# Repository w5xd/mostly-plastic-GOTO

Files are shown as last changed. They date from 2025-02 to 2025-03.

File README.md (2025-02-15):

<h1>Mostly Plastic GOTO for my Mostly Plastic Telescope</h1>

<pre>
Credits: 
    @Maff at https://kissner-optik.netlify.app/ for the Hadley and Caroline projects.
    3D model for GT2 pulleys I very slightly modified from http://www.thingiverse.com/thing:16627
    3D model for threaded screw and bolt holes using https://github.com/rcolyer/threads-scad
    the MCAD library for involute gears as distributed with Openscad
    at least one STEP model for a hardware item from http://mcmaster.com
    OnStepX at https://onstep.groups.io/g/main/wiki
    at least one STEP model for an electronic part from http://digikey.com
</pre>
Each of the above has its own license for sharing and attribution.  

This repository hosts 
the design of a GOTO stepper system for my mostly plastic 6 inch telescope, the Caroline
variant of the easy-to-build 4 inch Hadley telescope. The files here are licensed according to <a href='LICENSE'>LICENSE</a> by me, Wayne Wright. 
My GOTO design's key components are these 3D printed parts:
<ol>
<li>26:1 planetary gearbox with NEMA17 input. Printed in Prusament PC Blend
<li>200 tooth Azimuth pulley, printed in Prusament PC Blend, threaded to an M10 bolt anchored to the 
stationary plywood base of a dobson mount. 
<li>300 tooth Elevation pulley, printed in PETG, with 4 hole bolt pattern matching the Caroline rocker fasteners. 
</ol>

<h2>Introduction</h2>

I started my telescope experience with @Maff's post on printables.com: 
https://www.printables.com/model/224383-astronomical-telescope-hadley-an-easy-assembly-hig.
I first built a Hadley four inch telescope, and then its six inch Caroline variant, hoping to see some views in the night sky from my not-very-dark
suburban location. They work! Jupiter and its moons and Saturn with its rings are easily viewable from my yard with my mostly plastic telescopes. 
Now I want to find some dimmer objects. It turned out that my ability to navigate the night sky is
a limit. I recognize too few landmarks in the sky to find my way to any dimmer objects with any consistency. 
Herein is the GOTO
capability I added to my Caroline expecting its motorized mount could guide its view to, for example, Uranus, 
which I have failed
to find using manual pointing of my telescope.

To learn about motorizing it, the Hadley  discord server (https://discord.com/invite/ycaa8nX7sa) thread 
"Robo Hadley, Caroline and Bradley" has a pinned post with a design
(https://www.dropbox.com/scl/fo/ixfjrd8yioju8qfbt7a6b/AAvlGwa43vOzdwPsX5inDz8/Hadley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  login required)
involving a number of belts and pulleys and ball bearings.

But that design requires different and more sophisticated woodworking than what I already had. 
I decided to try my own that achieves, I am sure, less precision, but adequately points my Caroline
while effectively minimizing the changes to my familiar plywood Dobson mount. 
 I add (alot of) 3D printed plastic parts, including a planetary gearbox, commonly
available items like machine screws and nuts, various sizes of ball bearing assemblies and two GT2 by 10mm wide belts. 

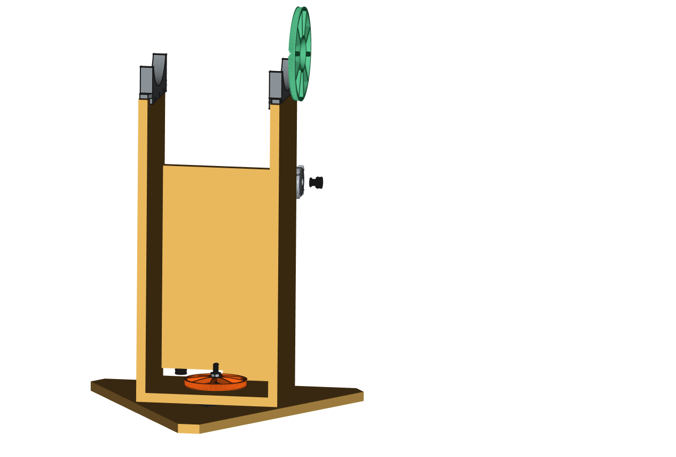
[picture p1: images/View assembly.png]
View Assembly


The plywood pieces in the drawing are from my original non-motorized mount for my Caroline. They survived intact save some
new holes.  The 3D printed cradles (in PETG) 
that mate with the Caroline's rockers are of my own design (cradle.stp) that I used on my original. Because my plywood 
cutting skills are limited, I 
tweaked the width of the cradles, printing multiple iterations, until I had a pair that held the rockers to less than about 1mm of play along
the elevation axis. In the original hand-actuated implementation the extra play was a "don't care" but I reprinted to reduce the play for the motorized version expecting
to put microswitches to trigger at the elevation limits. However, I have yet to place such limit switches as I have not found a need. The drawings above and below
emphasize the added components for GOTO capability. The elevation pulley bolts onto the Caroline original rocker arm using the original bolt pattern, 
but with longer, 10-24 x 1 1/4" bolts. The azimuth
pulley is fastened to the vertical M10 bolt that serves as the axis around which the upper box rotates.

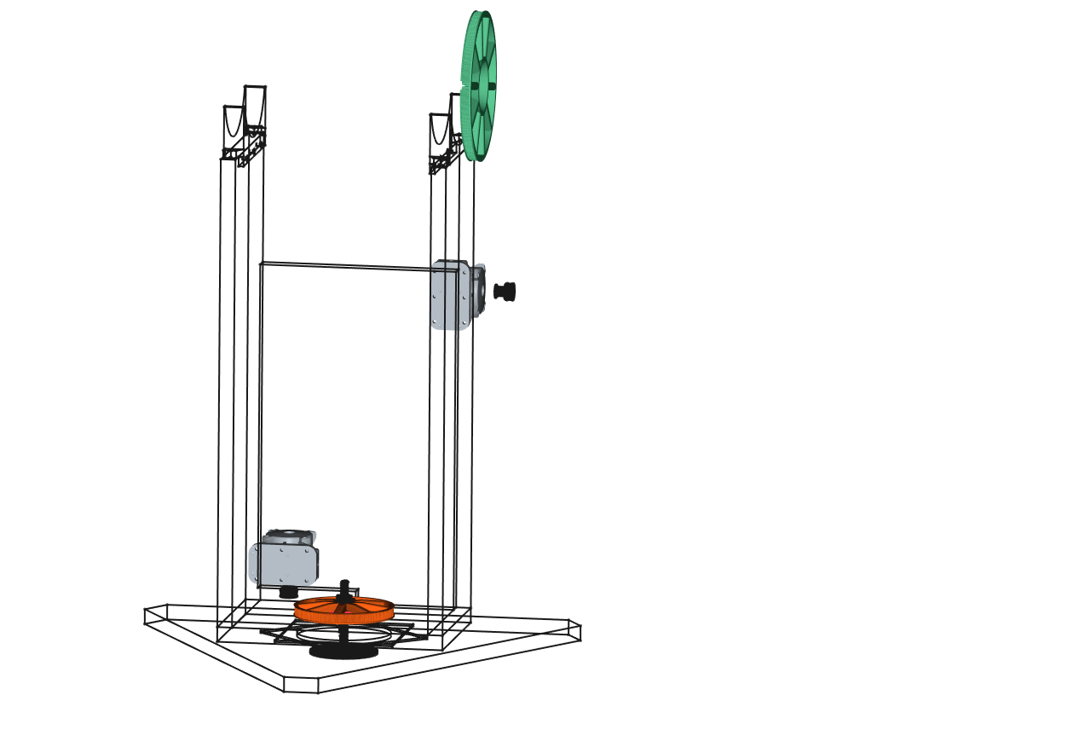
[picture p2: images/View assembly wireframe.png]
View Assembly Wireframe


The power trains for the two axes are similar to each other, but mine are not quite identical mechanically: 
each has a NEMA-17 stepper into a 3D printed 26:1 gear reduction 
box. As can be observed
in the wire frame view above, the gearboxes are mounted
to the front of the dobson mount. In my build, for the elevation axis I used a 200-step-per-revolution NEMA-17 I had left over from a 
3D printer upgrade. For
the azimuth, I bought a 400-step-per-revolution NEMA-17 from Amazon (https://www.amazon.com/dp/B0B8HB5N4S).

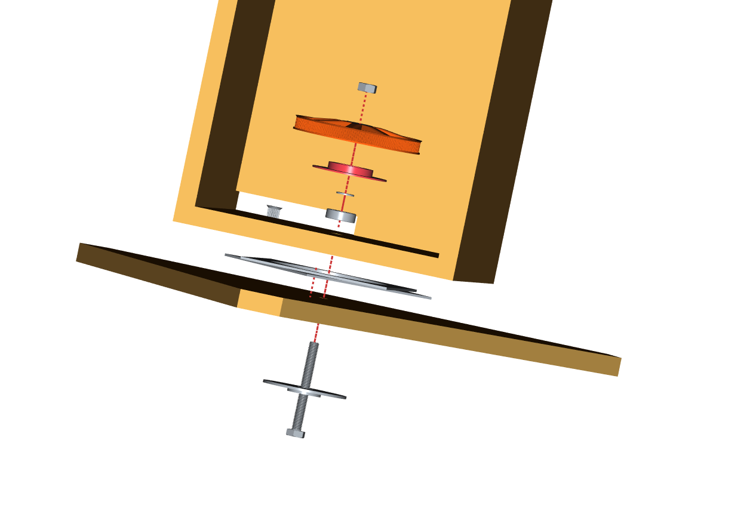
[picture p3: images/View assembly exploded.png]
View Assembly Exploded


The assembly of the azimuth axis, from the bottom up, is:
<ul>
<li>a M10 x 90mm fully threaded hex head bolt, which passes first through ...
<li>... the Azimuth Bearing M10 lock printed part.
<li>The stationary triangular plywood base
<li>An inexpensive lazy susan turntable bearing from Home Depot (https://www.homedepot.com/p/Everbilt-6-in-Square-Lazy-Susan-Turntable-with-400-lb-Load-Rating-49548/203661089)
<li>A 6200 roller bearing, 10mm ID, 30mm OD, 9mm thickness (https://www.amazon.com/dp/B07FVZMKP2)
<li>An M10 x 18mm OD x 1.5mm thick flat washer
<li>The Azimuth Bearing Holder printed part.
<li>The OnStep Azimuth Pulley printed part
<li>An M10 hex nut.
</ul>

Not shown in the drawings are the two 10mm wide GT2 belts. The elevation axis takes advantage of the fact that only a bit more than 90 degrees of
rotation are required and so can have a cut-to-length belt that is anchored in slots on the 3D printed azimuth pulley. I bought this 10mm
wide GT2 belt from Amazon and cut it: https://www.amazon.com/dp/B0CPT9J8QB

<h3>Azimuth Axis</h3>

The azimuth axis rotates all the way around therefore requires a closed loop belt. I used a 610mm by 10mm wide belt from Amazon
(https://www.amazon.com/dp/B0BYWVKM8T).

<h3>Elevation Axis</h3>
The important detail regarding the elevation pulley is that it has a tapered, GT2-compatible slot that holds the two ends of the
cut-to-length elevation pulley. 

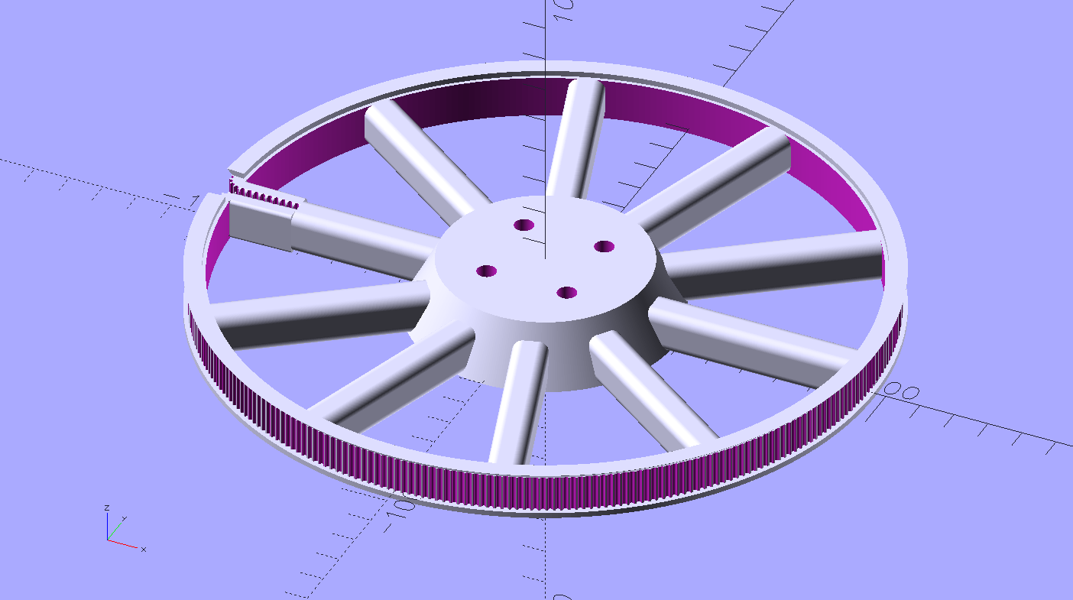
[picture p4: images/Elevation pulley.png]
Elevation Pulley


<h2>Notes for the prospective builder</h2>

As of this writing, only one of these GOTO mounts has been built: mine. The author makes no claims about how reproducible this design might be, nor for
any specifications it might meet. It worked for my own purposes. The author also makes no claims or even comments about how or whether
this design could be modified or extended, save this one: while the Hadley rocker arms have the same bolt pattern as Caroline and
therefore could mate this elevation axis unchanged, this 200 tooth azimuth pulley with its 610mm belt for the Caroline are too big to 
fit the slightly smaller plywood mount which holds my 4 inch Hadley. I have no plan
to motorize my Hadley, however, because I want to keep a telescope that doesn't require a battery.

At this time, I am not publishing printable STL files because I don't have any now that I am willing
to support or maintain over time. You will need to install and run <i>a recent version of</i> openscad to generate the printable files for the
GOTO mechanical parts. Scroll
this page https://openscad.org/downloads.html down to the Development Snapshots. (I used OpenSCAD-2024.12.04-x86-64.) The Windows cmd files to
invoke openscad with all the necessary parameter settings are published here. If you want to build from my electronics enclosure designs, then you'll
also need FreeCAD from http://https://www.freecad.org/.

As expressed in formal language in <a href='LICENSE'>LICENSE</a>, the author here places no further restrictions on anyone 
to publish derived works, <i>e.g.</i> STL files or a bill of materials for building this design. All
the sources for the 3D printable models are either of my own design and in this github repository, or are taken from somewhere that is documented
with a URL. There is more commentary in the scad files that I strongly recommend reading if you want to build this.

I describe what material I used to print each piece because I suspect that choice makes a difference in 
how some of these parts function, especially the gear box, but I don't have any recommendations about what
materials to use.

<h3>Azimuth axis assembly</h3>

My non-motorized Caroline used to turn on a 1/4-20 bolt centered through the stationary plywood base. I enlarged the existing holes for the M10 bolt in this upgrade, but I used two different twist drill sizes.
<ol>
<li>I drilled the fixed base with a 3/8" bit, which gives a tight fit to the M10 bolt, which will self-thread into the 3/8" hole.
<li>I drilled the base of the rotating plywood box with a 1/2" bit, which passes the M10 bolt without contact.
<li>The printed part, in PETG, using STL from Azimuth-Bearings.scad with its "part" set to "M10 bolt lock" tightly press 
fits over the hex head of the M10 
bolt. This bolt lock has
holes for wood screws that lock the M10 bolt hex head from turning.
<li>The lazy susan turntable needs to be centered on the M10 bolt. I designed a jig, lazy_susan_jig.scad. (This I printed in PLA--the part is
disposable.) The jig centers the turntable axis on the M10 bolt. Of course the bolt needs to already be in place in the 3/8" drilled hole for the jig
to center the turntable. I used #6 x 3/8" sheet metal screws to hold the turntable to the stationary plywood base. There are no fasteners between the 
turntable and the rotating upper plywood box. It's the M10 bolt assembly that holds the entire thing together. I left the 3D printed centering jig in place because it didn't hurt anything,
even though it is non functional once the wood screws are placed through the lazy suzan.
<li>The rotating plywood box fits loosely over the M10 bolt next.
<li>The 10MM ID bearing is next. Its ID does not fit snugly on the M10 bolt threads, but this design needs lateral stability across that axis.
Therefore, before placing the bearing, I wrapped (and wrapped and wrapped) Teflon pipe thread tape
around the mating portion of the M10 bolt to enlage its diameter to make the bearing snug.
<li>A 1.5mm thick M10 flat washer, 18mm OD goes next.
<li>The printed part using Azimuth-Bearings.scad with "part" set to "Bearing Holder" printed in PETG. It is anchored into
the plywood with three sheet metal screws.
<li>The Azimuth pulley is printed (in Prusament PC Blend) with M10 threads in its center hole. It threads onto the M10 bolt. It needs to be
tight enough to hold the stationary base to the rotating base together when the pair is lifted, but not so
tight as to apply undue pressure to the lazy suzan bearings, which makes them stickier.
<li>Finally, an M10 nut is threaded down snug against the (threaded and plastic) Azimuth Pulley. The nut is tightened enough to keep the Azimuth pulley from
unthreading when the stepper motor drives it clockwise. The metal nut against plastic threads can destroy the plastic, so I just tightened it
until the pulley didn't wiggle when I tried to turn it against the stationary base.
</ol>
Author's note on that final item: Designing M10 threads into the 3D printed pulley was the last of several failed iterations  
that tried M3 set screws
 to hold the pulley locked against the M10 bolt, <i>i.e.</i> it wasn't as easy I had hoped to lock the azimuth pulley to the fixed base's
M10 bolt.

<h3>Elevation Axis Assembly</h3>
To mount the pulley to the 'scope by removing the 4 bolts in the square pattern that hold the existing rocker,
replace the bolts with slightly longer ones, 1 1/4" long. The belt locking slot <i>must</i> be placed at the 9 o-clock position while the telescope is vertical
with the rotating part front (with the gearbox mounted) to your right.

My technique for getting the proper belt length was to first permanently mount the elevation gearbox's cleat and 
temporarily hang the gearbox on the cleat at its most vertical position. I cut a length of belt that was a couple of inches too long, and then
trimmed just a few teeth off the belt at a time until it was just long enough to enable mounting/dismounting the elevation gearbox from 
its cleat with the 8-32 x 2" tightening screw fully loosened.

<h3>3D printing</h3>
I printed all the parts of the gearbox, except its mounting cleat, using Prusament PC Blend. I also printed the azimuth pulley in PC Blend.
The rest of the parts were printed in PETG. I tried to print the elevation pulley in PC Blend, but could not overcome problems with it warping.
(It nearly fills the MK4 print bed, and I gave up when my print failed at
75% when it warped while well-bonded to the steel PEI coated sheet
and pulled the steel sheet off its magnets like a potato chip, and triggered my MK4's "filament stuck" logic--haven't seen that happen before.) 
I am using one printed in PETG. I printed all the parts on a Prusa MK4S or MK3.9S 
with a 0.4mm nozzle, and with PrusaSlicer set to 4 perimeters. I printed (almost) all the parts with a 5mm
brim. Some of the parts require a support volume when sliced, and in those cases there is an option in the scad file to
export the necessary support volume.

To successfully build the gearboxes, you <i>will</i> learn about how to confirm the correct extrusion width on your printer. If you don't already know
how, I recommend Prusa users start here: https://help.prusa3d.com/article/extrusion-multiplier-calibration_2257. Here 
is a photo of the boneyard from my gearbox printing.

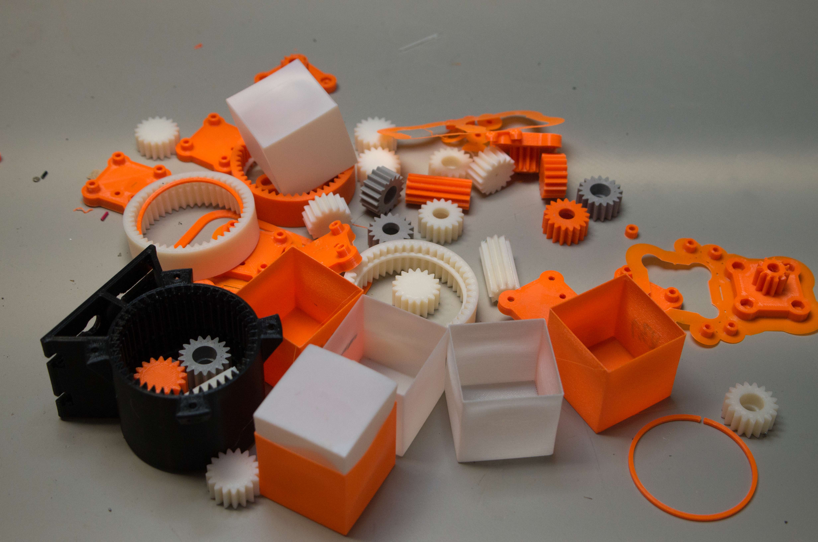
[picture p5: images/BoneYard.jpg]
Bone Yard


The scad file has an option to generate test versions of the main gearbox pieces that
have all the critical geometry and can be printed in a couple of hours. Maybe that
will help a future builder avoid further populating the plastic graveyard. See below.

Once I got my printers calibrated, the wall thicknesses of the test cube were within 5% of the required 0.45mm measurement described in the 
extrusion multiplier test. My own experience: A brand 
new "high flow" 0.40 mm nozzle came with my MK3.9S upgrade it. Nothing I did in the slicer got the test cube wall thicknesses anywhere closer 
than 10% too thick.
Finally, I swapped one of my old 0.40 mm standard brass nozzles back onto the newly upgraded printer. Then the next test print was within 5%. After that, I was able to print on both my printers without
modifying default extrusion parameters in PrusaSlicer and the gearboxes meshed well.

<h4>Gearbox</h4>

OnStepGearReducer.scad is the source for all the components of the gearbox. 
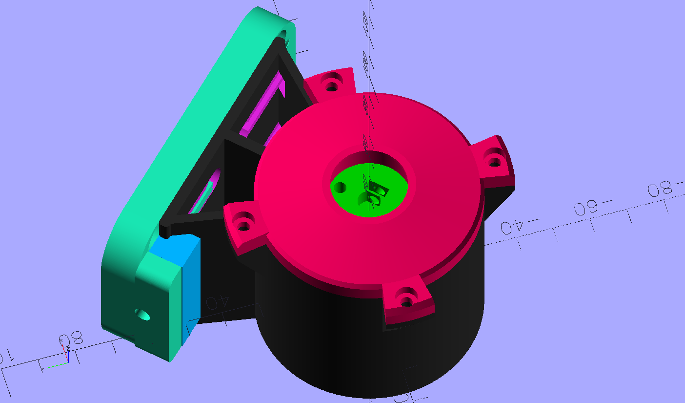
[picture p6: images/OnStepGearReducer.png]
OnStepGearReducer

MakeGearboxStl-TwoStage.cmd is a Windows batch file
that creates the various STL files from the scad. The gearbox has two internal stages, each stage giving a reduction ratio of 56:11 (or 5.0909...), 
which is about 26:1 overall. 
The scad file
has more commentary about how to print and assemble a gearbox.
The cmd file also outputs a set of four much simpler test STLs to verify printing of shapes of the outer ring, both the "planet"
and "sun" gears, the planet carrier, and the retaining ring. I found that once I could print
those test part, press the test prints and put them together and spin the gears with an appropriate amount of force,
the full feature parts would print routinely. Also in OnStepGearReducer is an option to invoke Openscad's animation feature
on the test model so you can watch the model of the gears turning. Here are the test parts:

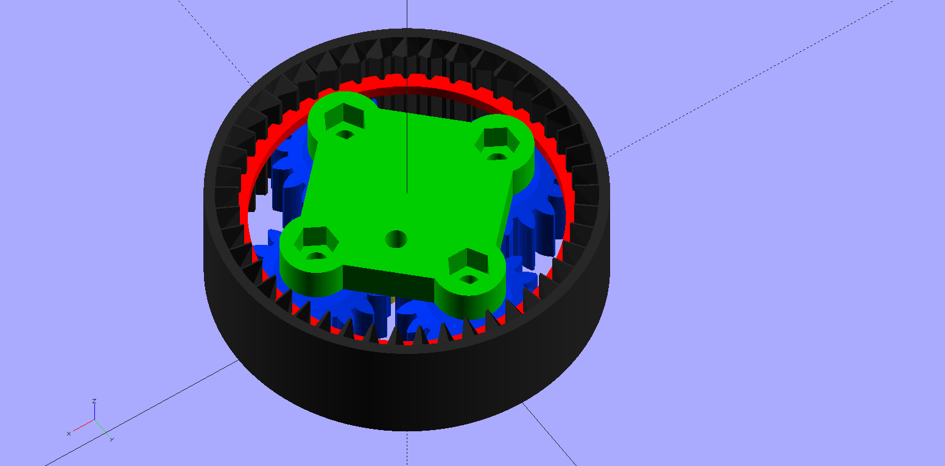
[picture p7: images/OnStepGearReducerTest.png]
Gearbox test


Each gearbox requires quantity 8 of 3mm ID by 10mm OD by 4mm thick bearing (623-2RS, https://www.amazon.com/dp/B0CLY7NJJ4). 
Each bearing is fastened by an M3 x 12mm socket head screw and M3 hex nut. And blue Locktite on the nut threads. Mine
disassembled themselves without the Locktite. After I assembled and tested that the gears would operate properly,
I disassembled and greased the plastic-on-plastic bearing surfaces with white lithium grease.

The gearbox housing is held to the cleat by the four screw heads that slide in
the gearbox slots. The printed threads are for #8 x 1/2" machine screws. 

<h4>Gearbox Output</h4>

The output of each gearbox is a length of D-profile 6mm diameter flatted shaft with a 5.5mm thickness measured to
the flattened edge. 
I bought these from Amazon and cut them to length: https://www.amazon.com/dp/B0C274W667.
The length is enough to hold the 20 tooth gearbox pulley. The STL part is from OnStepGearBoxElevationPully.scad. 
It's the same part on the azimuth gearbox as well. The inner carrier prints with a D-profile 6mm hole that should have a cut-to-length piece of steel shaft
inserted to keep it stiff against the rotational stress that it takes across the weakest grain of the
3D print.

Several M3 square nuts are required for the locking screws into the flats of the pulley shafts, and a couple of M3 socket head screws are
required. They can be set screws of at least 4mm length, but there is alternatively room for a longer socket head
screw of about 8mm. The output bearing housing, containing a 636-2Z bearing(https://www.amazon.com/gp/product/B081JSWT49), 
fastens to the outer ring with quantity four of 
M3 x 8mm socket head screws and mating M3 hex nuts. (A longer M3 screw is useful to first pull the nut into the well of the housing.)

<h2>Electronics</h2>
The electronics I used were unique to my situation. I record what I did here for completeness, but I recommend to anyone getting
this far into this project to consider using a more off-the-shelf electronics design. I bought an assembled OnStepX 
capable MaxPCB4E from https://graydigitalarts.com/product/maxpcb4e/.  I did not install the web server 
Teensy that
board supports because I only want to control my telescope from the OnStep Android app via 
Bluetooth. https://play.google.com/store/search?q=OnStep.
I bought this HC-06 bluetooth-to-serial 
device, https://www.amazon.com/dp/B07VL6ZH67, and jumpered the necessary four wires on the MaxPCB4E to it. 
The four wires are +3.3V, Ground, and TX2 and RX2 to the main Teensy 4.1 per this
diagram: https://oshwlab.com/hdutton/maxpcb4e

I did not find an appropriate enclosure for the OnStep PCB, so I designed and printed this one: OnStepEnclosureAssembly.FCStd in PETG.
I used a 9 pin Molex connector for the necessary 8 wires to the stepper motors. (Why a Molex? because I had the connectors already,
and I prefer a setup that cannot reverse the azimuth/elevation axis stepper connections.)

I decided to power my OnStep with a battery pack of eight D cells held by a pair of these
4X D-size plastic battery holders: https://www.mouser.com/ProductDetail/12BH143A-GR.
The nominal 12V DC from a full battery pack is boosted to 14V by this boost converter from Amazon. https://www.amazon.com/dp/B0C6FF1P41.
 The boost converter allows for populating the 8-position battery holder with fewer than 8 cells as long
as each cell-less position is occupied by a dummy D cell (a D-cell sized device that presents a short circuit.)
There exist 14-packs of alkaline D cells for sale, which means the booster makes it practical to use those 14 in two
batches of 7.
With my particular stepper motor amperage requirements (about 1.5A each), the internal resistance of even brand new
D alkaline cells makes six cells the fewest that will deliver the necessary amperage for that chemistry. The
boost converter also makes the system less sensitive to the battery chemistry such that, for example,
rechargeable D cells will work, and maybe fewer than eight if the builder prefers. Of course,
using fewer cells in the battery also means a shorter battery life.
The battery back and boost converter fit in this enclosure of my design: BatteryPackEnclosure.FCStd
Measured current draw at battery with boost module only: 15mA. With boost module driving the OnStep, but no steppers: 85mA.

OnStep supports limit switch input and I designed this little part, LimitSwtichBracket.FCStd, but I have not installed,
nor wired it up because I don't mind watching for a problem as the telescope moves, and,
once calibrated, OnStep won't command it to run into a stop anyway.

The electronics enclosures I printed in PETG.

If you really want to duplicate the battery enclosure, you are going to find that I am a
FreeCAD novice and ended up with a model for the enclosure base with an embedded copy of
the 3D model of the boost converter (oops.) This is error is why the part to export for the enclosure base is a
mesh "Cut" operation whose name starts with "Repaired." The power switch in the battery enclosure is the same part 
as the
slide switch in the build-it-yourself <a href='https://www.thingiverse.com/thing:3017274'>ST4 project</a> referenced below.

As I noted above, there are better designs for OnStep electronics and enclosures than mine.

<h2>Modified ST4 box</h2>
I bought a PCB for this 3D printable box for an ST4 controller: https://www.thingiverse.com/thing:3017274.
I did not like the oversized empty thickness of the bottom side of the case, so I modified it here: stl_bottom_socket.FCStd

<h2>Final assembly and disassembly</h2>

Each gearbox assembly includes a cleat with a sliding axis to adjust belt tension. The cleat has 6 available holes for fastening to the 
front of the dobson box. Both cleats are mounted to the same side, the front side, of the rotating plywood box, one
for the elevation axis and another for the azimuth. I fastened using only 3 of the 6 holes with #6 x 1" wood screws. 
Each cleat has 4 threaded holes (#8 machine screw
thread) for 8-32 x 1/2" pan head screws that form the sliding axis for the gearbox. Belt tension is maintained
 with an 8-32 x 2" screw and mating hex nut
that is anchored in a hex hole in the cleat. The tip of the belt tension screw engages a mating hole in the (poorly named)
cleat lock printed part. The elevation axis has a cut-to-length belt (GT2 by 10mm wide). 
The sliding axis on the cleats has a limited range, so it's necessary to take some care with the exact placement 
of the azimuth gearbox 
such that it is possible to both install the 610mm belt and also to tighten it enough. 
The same limited range affects the length of the cut of the elevation belt.

Unscrewing the elevation axis belt tension is how to release the elevation belt so that the
 the telescope can be separated from the mount for transport.

<h2 id="Initialize_OnStep">Initial Bench Tests and Setup with OnStepX</h2>

This project was the first time I have used OnStep. The instructions I found on its wiki most relevant for beginning testing
were here: https://onstep.groups.io/g/main/wiki/3865. However, it was not obvious to me how to accomplish
the bit it says about 
<q>If your mount doesn't have clutches and you need to use OnStep to move to the polar home position.</q>

I connected an ST4 controller, and I thought I might turn on the power
and press a button on the ST4. Nothing happens. This is by design. It takes some learning about OnStep to figure
how how to get things started. I worked out the following by trial and error, and I list below the steps I took for
future reference. Put away the ST4 controller for later use because when you start, you don't know which way its
slide switches go for forward or reverse. I follow these steps every time even though the state of the OnStep
controller when you start may allow fewer button presses, this sequence always worked, at least for me:
<ol>
<li>With the OnStep controller powered up, and with the HC06 previously initialzed
 to a known name and password (see documentation for the HC06) bring up the OnStep Android app.
<li>Use the app's drop down menu to access its "Connection" item. Expect to start with Connection every time you either power down
the OnStep controller, or return your phone from outside of Bluetooth range.
<li>If this is the first time you have connected this phone to this HC06, you'll have to choose the correct Bluetooth name and
also enter its password. If you have connected before and are using the same phone and HC06, then the Accept button is enough because
the app offers the previously connected bluetooth address.
<li>The app should now be back to its top level screen. Press its "Initialize/Park" button. and then "Set Date/Time" and 
confirm you see its "Success" response. (I installed a coin cell for the Teensy's RTC
on my PCB, but I do this Set Date step everytime anyway as it otherwise
won't find the right stars later. I need to research whether that coin cell is supposed to keep time through
the loss of 5V to the PCB.)
<li>Back button on Android to go back to the app's top level app screen.
<li>Choose "Tracking" and then "Start." Then Back button on Android to go back to top level app screen.
<li>Choose "Guide/Focus" and now (finally) we can try to make the steppers turn.
<li>Use the drop down menu to set either of the speeds with "Fast" in its name (else it will move so slowly you can't tell its moving.)
<li>Confirm that the North and South buttons move the elevation axis, respectively, up toward the zenith and down toward the horizon. 
If this
is your initial test, be especially aware of whether you might have reversed the two axis' stepper wiring with each other, 
or that you may have
wired a stepper so that it moves in the wrong direction. Get all that fixed before you go any further. Confirm that 
East/West move the
Azimuth clockwise and counter clockwise, respectively. Again, fix this before going further.
<li>Use the Guide/Focus compass direction buttons on the app (or at this point you may use the ST4 instead) to move 
the telescope
to its "polar home position" which is at the horizon pointed north.
</ol>

When I initially tested on my work bench, I kept the main mirror cover in place and used only my finder to
roughly evaluate wheter, after a "Reset to Home" in the Initialize screen, that I could use "Guide/Focus" to
move to any elevation and/or azimuth, then return to the Initialize screen to command "Return to Home" and 
confirmed through the finder that the motors in fact move it back to home. After this, I connected my ST4
and confirmed it could move the telescope, and figured out what slide switch positions correspond with
forward and reverse.

In my first few nights outside, I discovered a few other helpful hints that I had not run across elsewhere.
 While the calibration process in the OnStep app can overcome the first two out-of-level
situations below,  as a beginner I found I was way better off always setting up the telescope level this way:
<ul>
<li>Use a level on the dobson base so the upper box rotates in a (close to) horizontal plane. I permanently fastened
an inexpensive bubble level (https://www.amazon.com/dp/B09KBG2ZNL) on the triangular stationary part, and installed leveling feet on it.
<li>Use a level on the telescope to make it close to horizontal before Reset To Home on the app. I fastened an
inexpensive bubble level (https://www.amazon.com/dp/B0D7HHCY9F) to one of the 1/2" AL telescope tubes. I designed and printed
a cylindrical object that mates the ID of the AL on one side, and OD of the level on the other (ScopeLevelHolder.FCstd.)
<li>There is a "Limits" entry on the app's main menu. That is where to go to allow the elevation to point the 
telescope to objects at the zenith (where the Moon was when I first tried and OnStep refused and I didn't know why.)
</ul>

With this mostly plastic GOTO setup, I have set OnStepX  "Backlash" setting at 400" for each axis. I have
not done any detailed work to adjust this Backlash setting.

<h2>Results</h2>
I am now sure I have seen Uranus through my Caroline. Anyone with experience with small telescopes will understand why
I have to say I can't unequivocally prove it. Uranus is just a dim dot in my eyepiece as this telescope cannot resolve its disk
through my light-poluted suburban sky. My
strongest argument is that I was able to GOTO to the Moon, Venus, Saturn and Uranus this week (in early February, 2025) while they 
were all within a few dozen degrees of each other in the night sky. The GOTO well-centered the first three 
in my 9mm eyepiece, and, when I did a GOTO to Uranus, there was a dim dot in the center. Stellarium said that
Uranus would be the brightest object in my telescope's 9MM eyepiece field of view, Q.E.D.

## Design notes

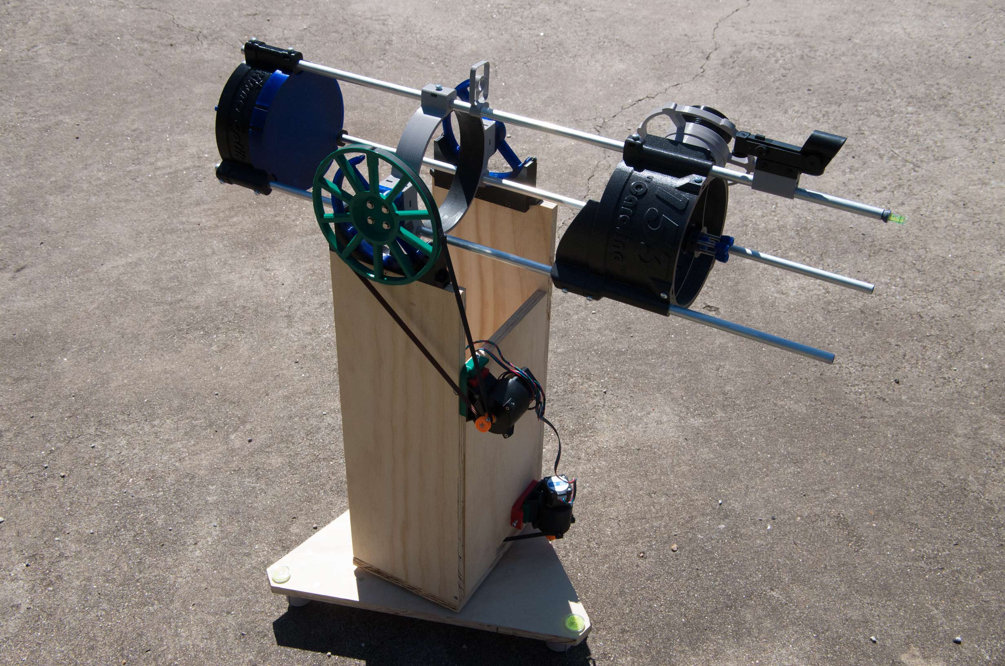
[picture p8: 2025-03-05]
images/photo-home-position-front.jpg

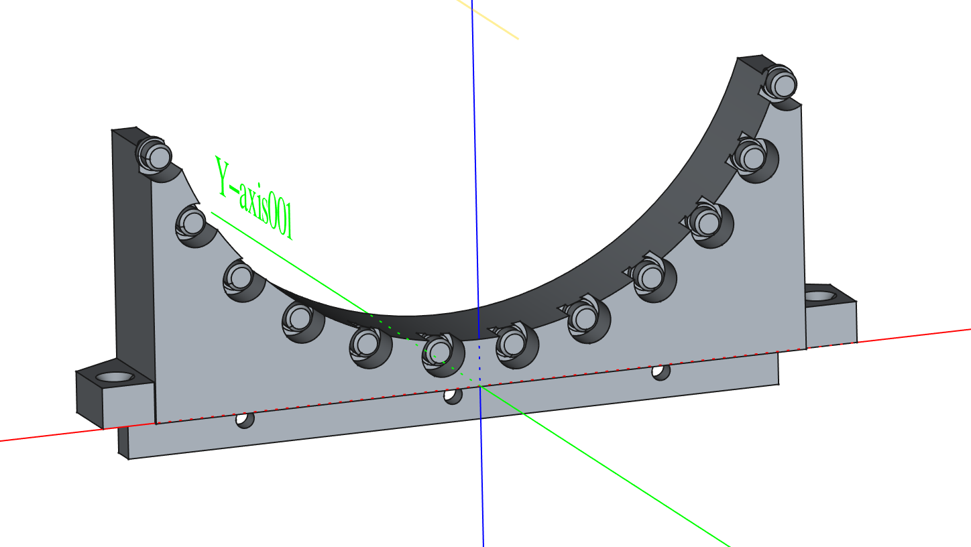
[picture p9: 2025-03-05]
images/Cradle.png

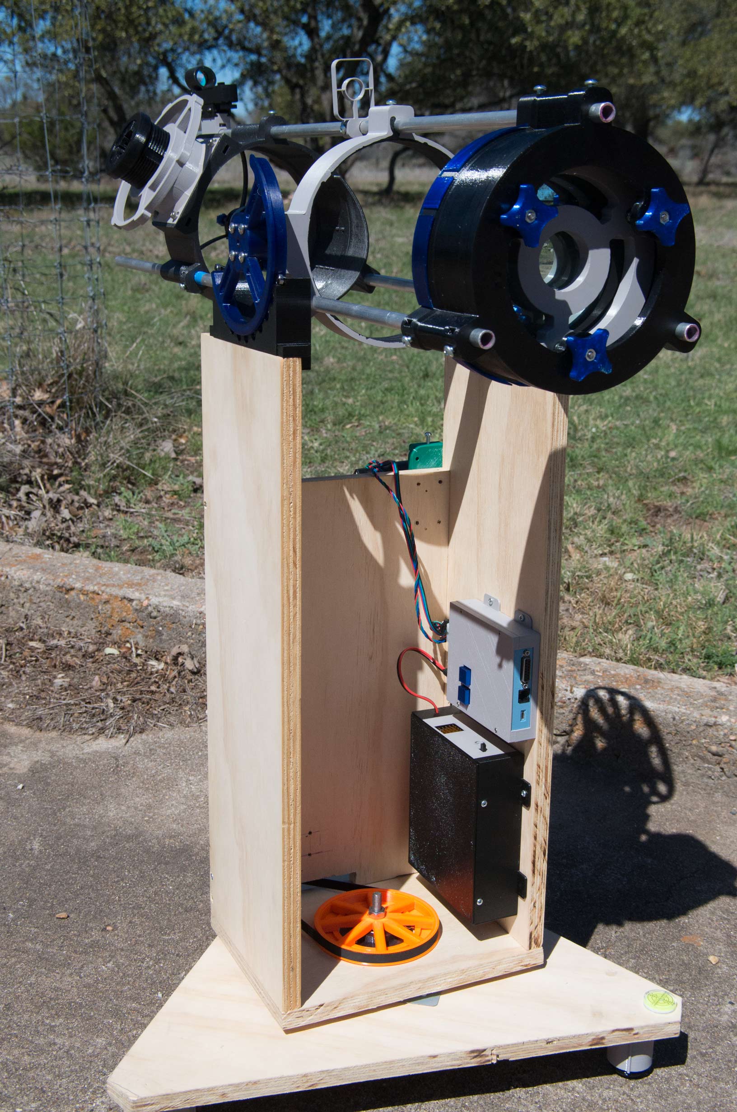
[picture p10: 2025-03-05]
images/photo-home-position-rear.jpg

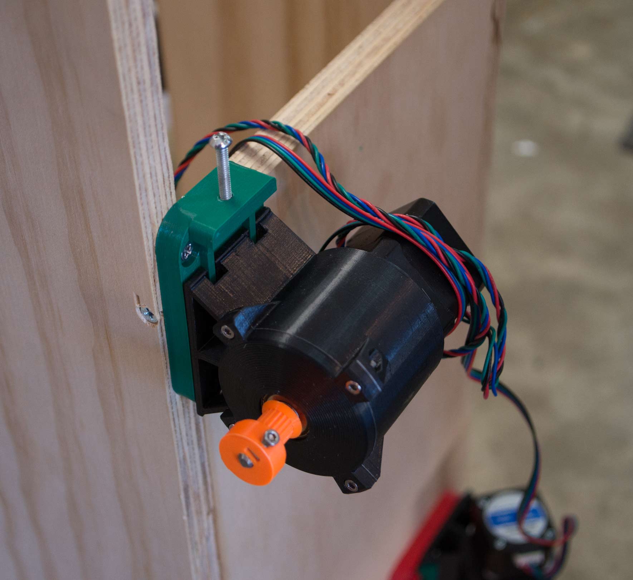
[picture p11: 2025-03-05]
images/photo-elevation-detached.jpg

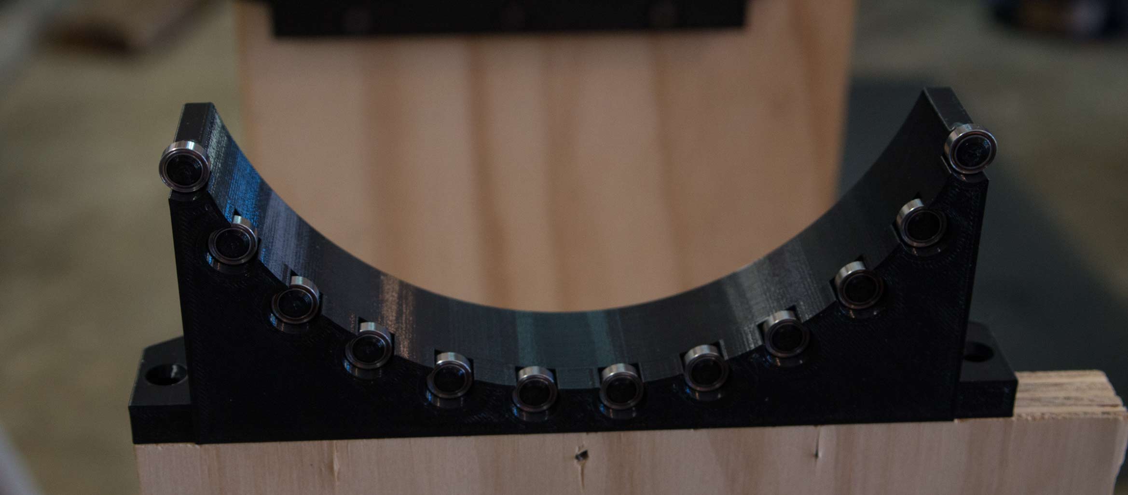
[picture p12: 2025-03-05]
images/photo-cradle.jpg

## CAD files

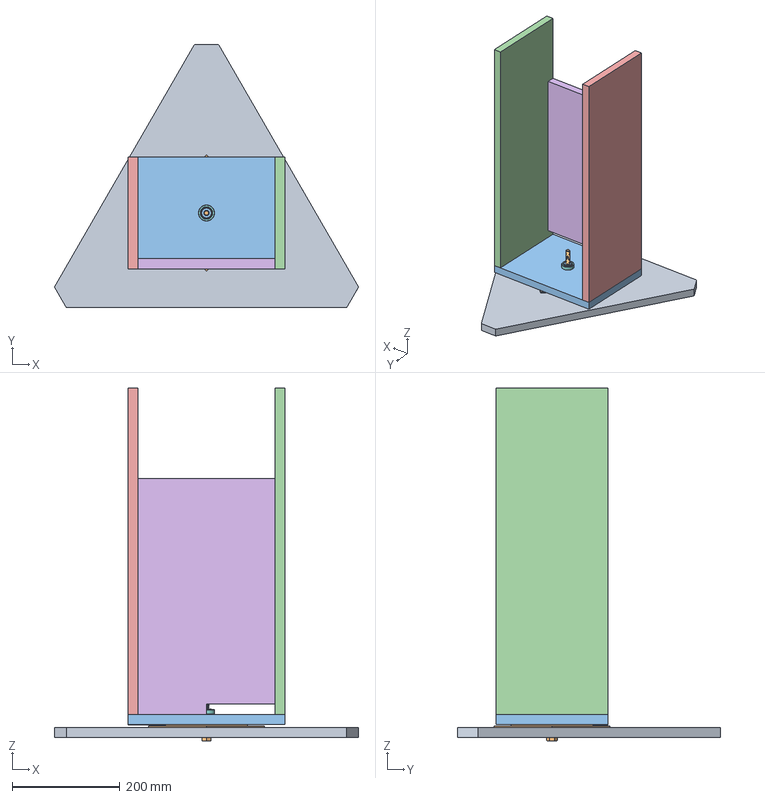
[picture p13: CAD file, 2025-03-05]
Caroline GOTO Assembly.FCStd
565.2 x 489.4 x 655.7 mm
base body
M10 x 90mm
bottom
SideR
SideL
Front
5972K101_Ball Bearing
5972K101_Ball Bearing001
5972K101_Ball Bearing002
5972K101_Ball Bearing003
5972K101_Ball Bearing004
5972K101_Ball Bearing005
5972K101_Ball Bearing006
5972K101_Ball Bearing007
5972K101_Ball Bearing008
5972K101_Ball Bearing009
5972K101_Ball Bearing010
M10 washer

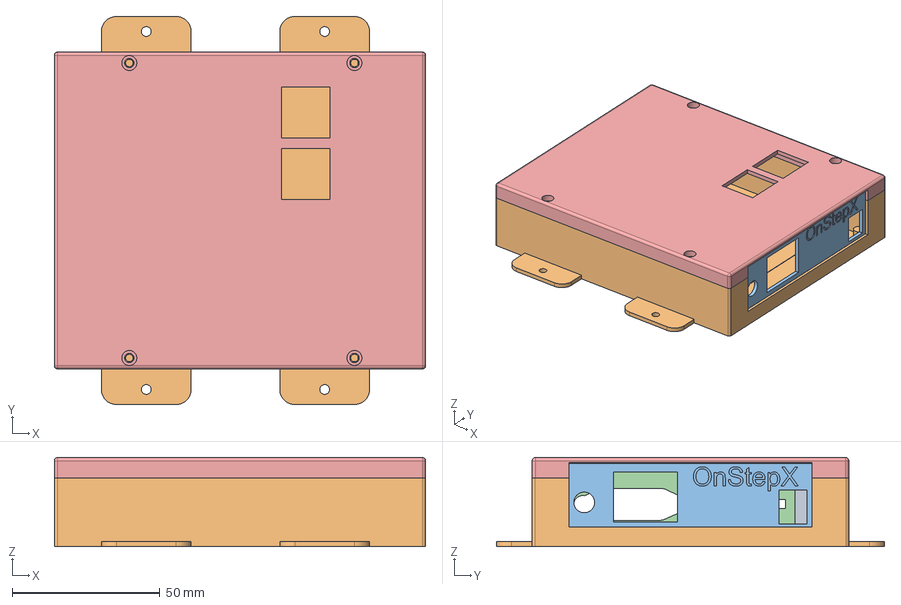
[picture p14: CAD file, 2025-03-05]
OnStepEnclosureAssembly.FCStd
125.7 x 131.3 x 30.1 mm
Fuse001
Enclosure Base
Enclosure Right
Enclosure Left
Enclosure Top

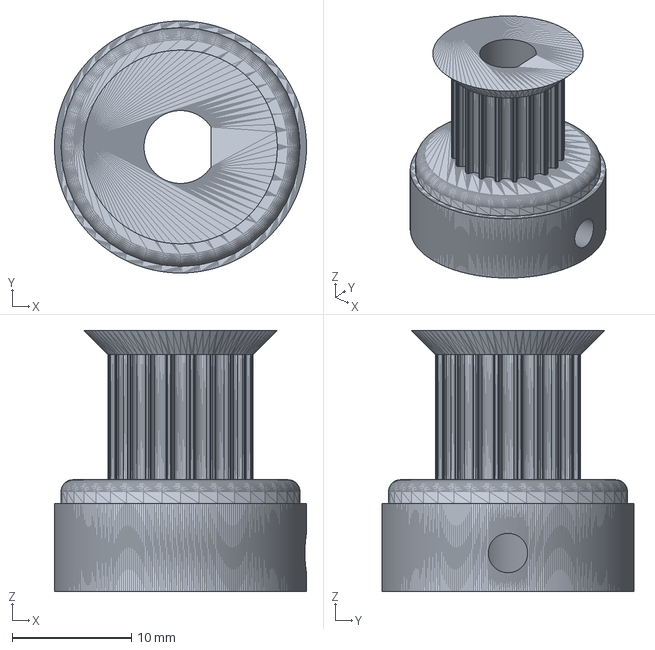
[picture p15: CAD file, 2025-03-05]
OnStepGearboxElevationPulley.FCStd
21.1 x 21.1 x 21.9 mm

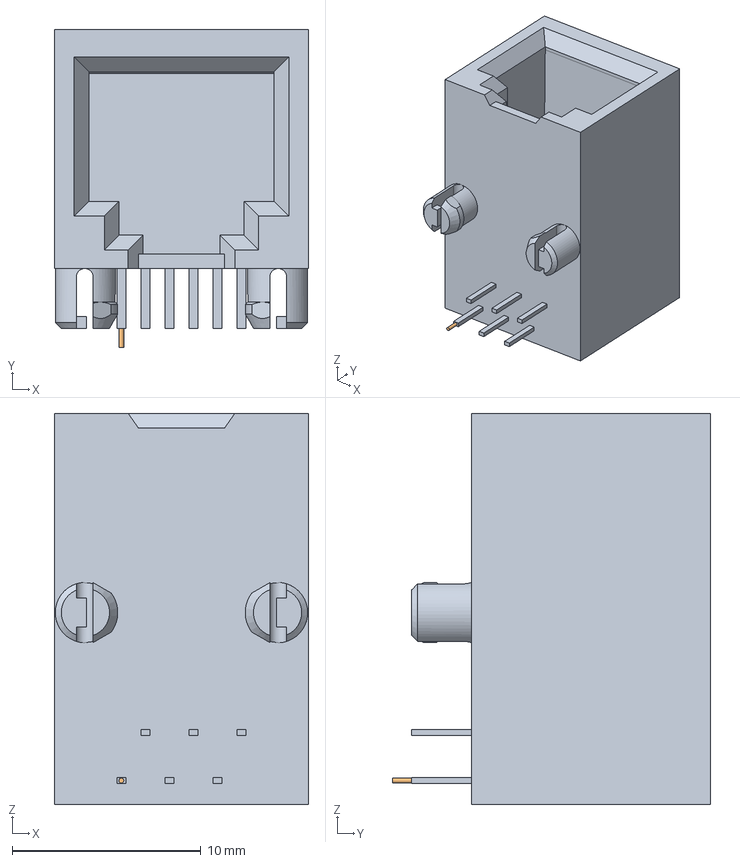
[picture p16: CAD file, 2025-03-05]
RJ12.FCStd
13.5 x 16.8 x 20.7 mm

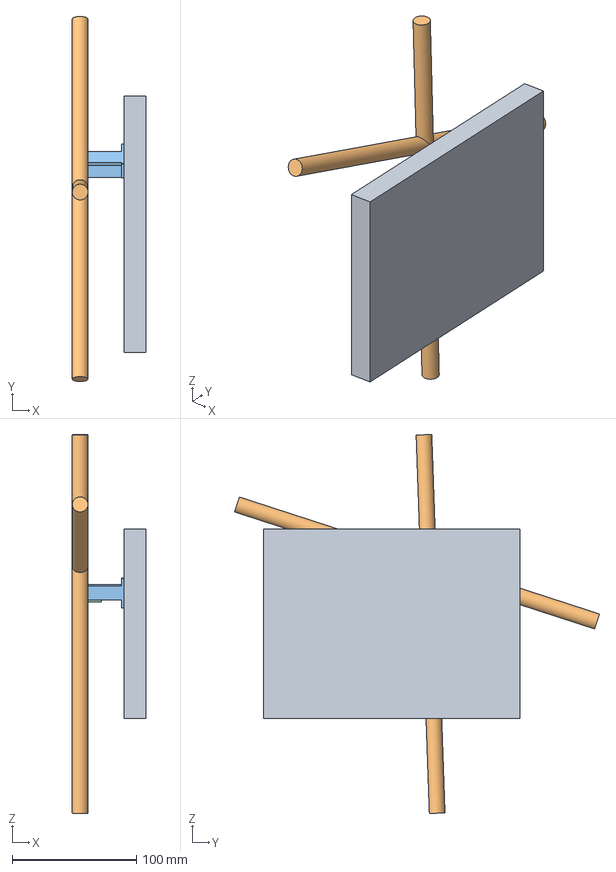
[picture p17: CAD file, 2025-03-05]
LimitSwitchBracket.FCStd
59.2 x 293.8 x 305.1 mm
Side Panel
Hadley half inch AL x 2
Bracket
Cover

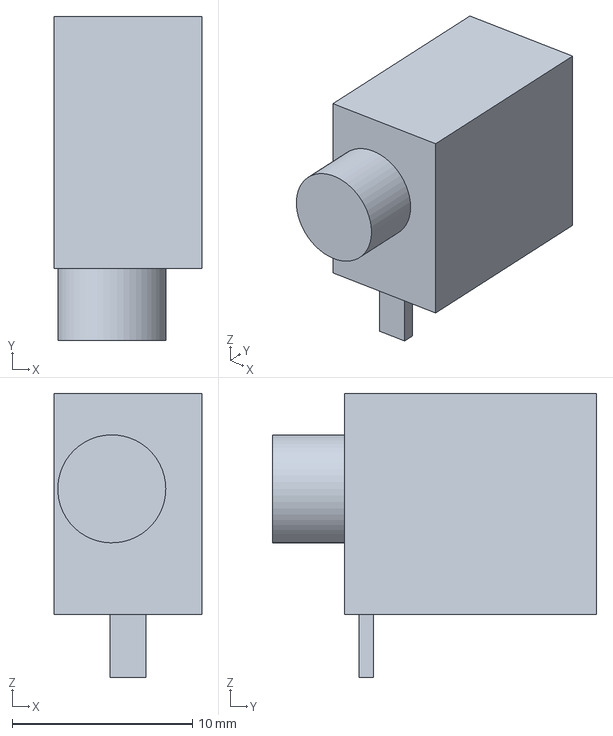
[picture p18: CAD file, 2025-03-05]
BoomEleC26230.FCStd
8.20 x 18.0 x 15.8 mm

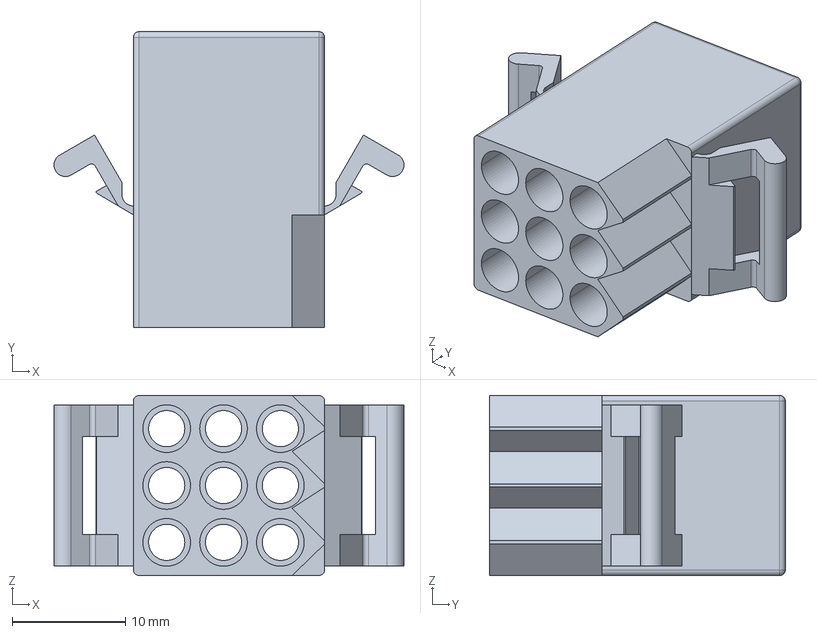
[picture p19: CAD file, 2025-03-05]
StepperMolex.FCStd
31.0 x 26.2 x 15.9 mm

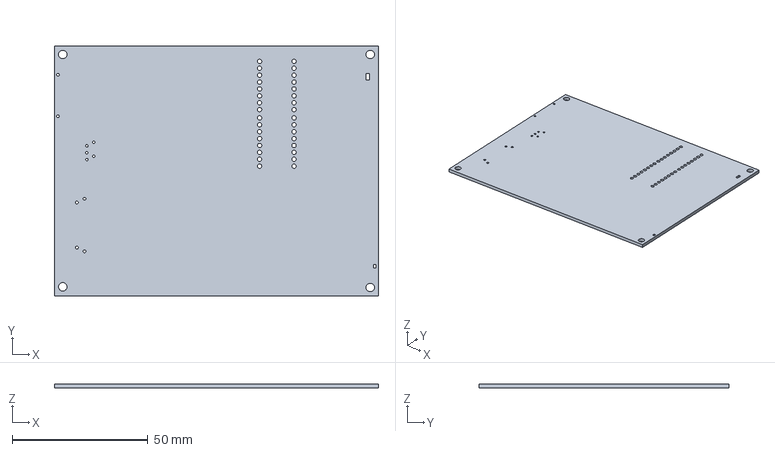
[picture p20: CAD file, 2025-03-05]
MaxPCBdxf.FCStd
119.4 x 91.9 x 1.59 mm

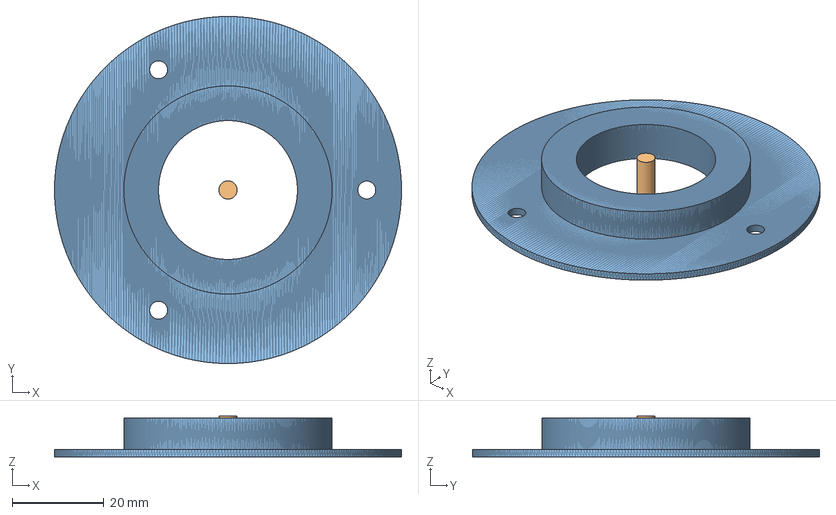
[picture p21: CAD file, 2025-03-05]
Azimuth-Bearing-Holder.FCStd
75.8 x 75.8 x 8.89 mm
Az Bearing Holder
Azimuth_Bearing_Holder001

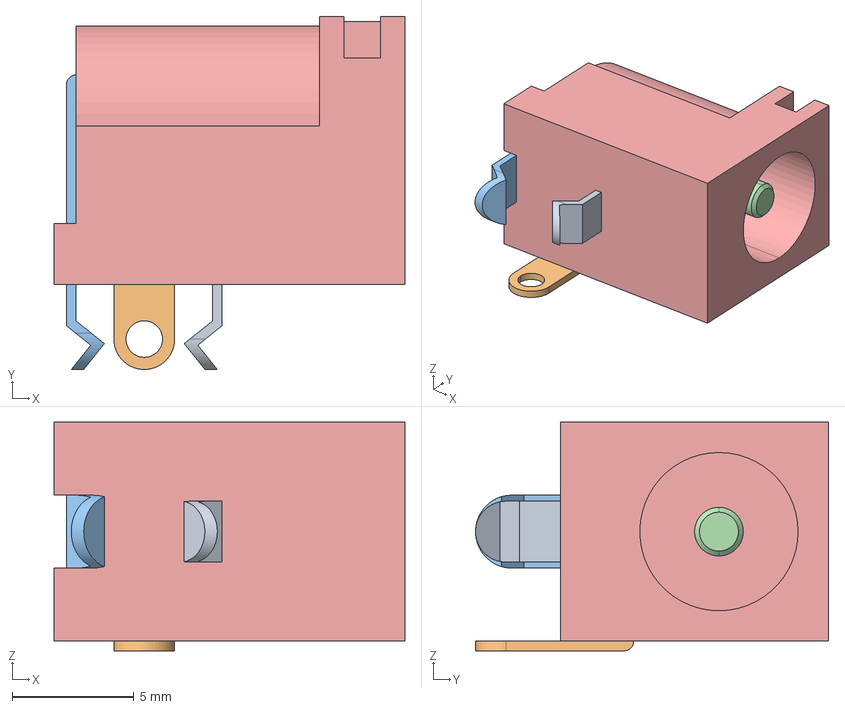
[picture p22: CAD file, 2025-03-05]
PJ202.FCStd
14.4 x 14.5 x 9.40 mm
PJ-202A_PJ-202A
PJ-202A_PJ-202A001
PJ-202A_PJ-202A002
PJ-202A_PJ-202A003
PJ-202A_PJ-202A004

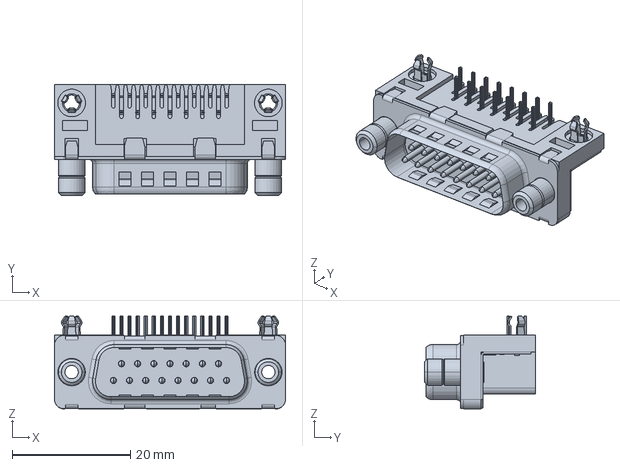
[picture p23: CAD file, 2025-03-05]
D15.FCStd
39.1 x 18.9 x 15.8 mm

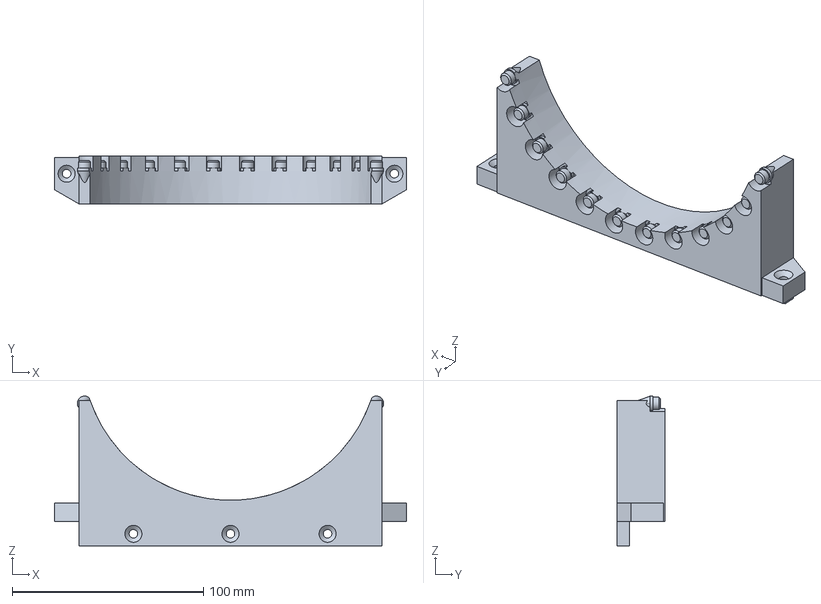
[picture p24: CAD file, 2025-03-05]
CradleBearings.FCStd
184.2 x 24.9 x 78.4 mm

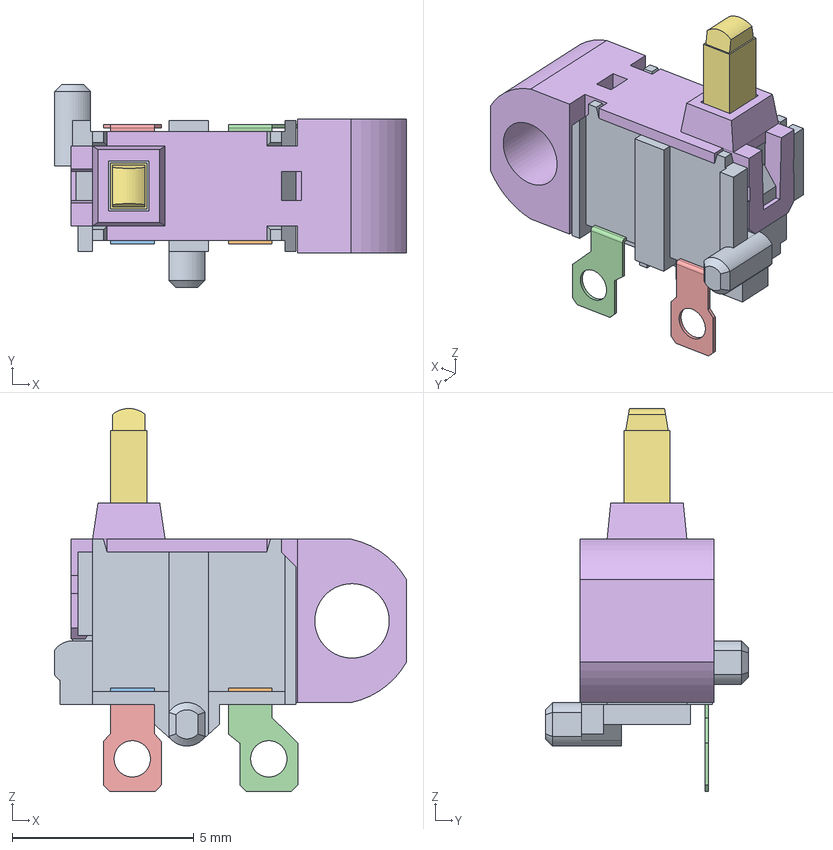
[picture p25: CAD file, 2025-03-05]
LimitSwitch.FCStd
9.70 x 5.60 x 10.5 mm
sw-3d-131-e11cs3-hs-pc-r00
sw-3d-131-e11ts8-hs-sk-r00
sw-3d-131-e11ts8-hs-sk-r001
sw-3d-131-e11ts8-hs-sk-r002
sw-3d-131-e11ts8-hs-sk-r003
sw-3d-131-e11cv9a-hs-sk-r00
sw-3d-131-e11lv9-hs-sk-r00

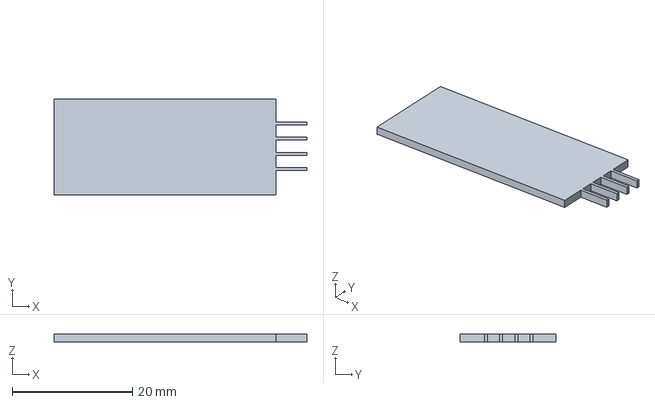
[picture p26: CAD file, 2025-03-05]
HC06.FCStd
42.1 x 16.0 x 1.27 mm

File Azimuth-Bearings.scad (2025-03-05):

/**************************************************************************
   Azimuth bearings (c) 2025 by Wayne E Wright,
   https://www.thingiverse.com/wwrr55
   is licensed under Attribution-ShareAlike 4.0 International. To view a
   copy of this license, visit
   http://creativecommons.org/licenses/by-sa/4.0/
*****************************************************************************/

echo("Azimuth-Bearings.scad version 1.0");

/* Printable parts for the Azimuth bearings on a Hadley telescope.
** They are fasteners and supporting mounts for a two-part plywood mount of the sort shown in this video:
** https://hackaday.com/2022/11/04/3d-printed-newtonian-telescope-has-stunning-looks-hadley-breaks-the-bank/
** The plywood parts are (a) the base that sits on the ground and (b) the upper part that turns 
** as the telescope moves in the azimuth direction. In the video above, the building uses a lazy susan
** bearing. 
**
** The bearing design here is not of the lazy susasn design. It instead offers a mount point for
** a pully to install an OnStep-based mechanism for a stepper motor to rotate in azimuth.
** The plywood parts here, instead of the lazy susan, simply have a drilled center hole in the two
** parts. The center hole in the plywood base is drilled for a tight fit for an M10 bolt, and
** the corresponding center hole in the rotating part of the mount is a larger hole, 0.5", to pass
** that same center bolt allowing the top to rotate w.r.t. the bottom.
**
** The weight of the upper dobson rests on 3 x teflon pads (1" x 1" x 1/8" thick).
** The M10 bolt resists lateral movement and supplies axial force only when the mount is lifted
** to be carried, in which case it transfers the weight of the base as an axial load on the 6200 bearing.
** 
** Three parts to print. Bottom to top:
** 1) a lock insert for the head of the M10 bolt to keep it from turning. Fastens to the bottom of the base.
** 2) Mounting template for the three 1" x 1" x 1/8" teflon pads. This template also has a tight-fitting
** center hole to locate the M10. Fastens to the top of the base.
** 3) Mounting template for the 6200 bearing. Fastens to the top of bottom part of the rotating azimuth
** plywood. 
*/


part = 0; // [0:M10 bolt lock, 1:Teflon Skid Template, 2: Bearing Holder]

lockBoltAcrossFlats_mm = 17;
lockBoltHeadThick_mm = 6.6;
lockBoltr_mm = lockBoltAcrossFlats_mm / (cos(30) * 2);
lockBolt_scale = (lockBoltAcrossFlats_mm - .25) / lockBoltAcrossFlats_mm;
lockScrewDiameter_mm = 3.9;

teflonPadWidthmm = 25.9;
teflonPadHeightmm = 25.9;
teflonSkidToCenter = 0.5 * 5 * 25.4;
teflonPadThick = 25.4 / 8;
teflonSkidThick = teflonPadThick /2;
teflonSkidHorzWidth = 25.4 / 4;
teflonSkidSpokeWidth = 20;
teflonSkidVerticalGap_mm = 0.5;
teflonSkidBoltClearance_mm = 9.9;

bearingOD = 30.3;
bearingThickness = 9;

module __no_more_customizer() {}

$fa = $preview ? 15 : 1;
$fs = $preview ? 3 : .1;

module M10HeadLock ()
{
    difference()
    {
        lockThick1 =  floor(lockBoltHeadThick_mm);
        lockThick2 = 25.4 / 10;
        union()
        {
            cylinder(d = 2 * lockBoltAcrossFlats_mm, h = lockThick1);
            cylinder(d = 5 * lockBoltAcrossFlats_mm, h = lockThick2);
        }
        profile = lockBoltr_mm * [for (i = [0:1 : 5], a = i * 60)[sin(a), cos(a)]];
        translate([0,0,-.1])
            linear_extrude(height = lockThick1+.2, scale = lockBolt_scale)
                polygon(profile);
        // screw holes to mount
        for (a = [0,120,240])
            rotate([0,0,a])
                translate([lockBoltAcrossFlats_mm*2.1, 0, -0.1])
                    cylinder(h=lockThick2 + 0.2, d=lockScrewDiameter_mm);
    }
}

module TeflonSkidTemplate()
{
    difference()
    {
       union()
       {         
        linear_extrude(height = teflonPadThick - teflonSkidVerticalGap_mm)
            circle(teflonSkidSpokeWidth);
        for (a = [0,120,240])
            rotate([0,0,a])
                translate([teflonSkidToCenter, 0 ])
                difference()
                {
                    union()
                    {
                     translate([-teflonSkidToCenter, -teflonSkidSpokeWidth /2])
                        linear_extrude(height = teflonSkidThick)
                            square([teflonSkidToCenter, teflonSkidSpokeWidth]);
                        linear_extrude(height = teflonPadThick - teflonSkidVerticalGap_mm)
                            offset(teflonSkidHorzWidth)
                            square(teflonPadWidthmm, center = true);
                    }
                    translate([0,0,-.1])
                    {
                        linear_extrude(height = teflonPadThick)
                            square(teflonPadWidthmm, center = true);
                        translate([-teflonPadWidthmm,0])
                            cylinder(d=lockScrewDiameter_mm, h=teflonPadThick);
                    }
                }
        }
        translate([0,0,-.1])
            cylinder(d=teflonSkidBoltClearance_mm, h=teflonPadThick);
    }
}

module Bearing6200Holder()
{
    holderThick1 = bearingThickness - 0.5;
    holderThick2 = 25.4 / 16;
    difference()
    {
        union()
        {
            cylinder(d = 1.5 * bearingOD, h = holderThick1);
            cylinder(d = 2.5 * bearingOD, h = holderThick2);
        }
        translate([0,0,-.1])
            cylinder(d = bearingOD, h = holderThick1 + .2);
        for (a = [0,120,240])
            rotate([0,0,a])
                translate([bearingOD, 0, -0.1])
                    cylinder(h=holderThick1 + 0.2, d=lockScrewDiameter_mm);
    }
}


if (part == 0)
    M10HeadLock();
else if (part == 1)
    TeflonSkidTemplate();
else if (part == 2)
    Bearing6200Holder();

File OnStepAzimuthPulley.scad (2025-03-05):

/**************************************************************************
   OnStepAzimuthPulley (c) 2025 by Wayne E Wright,
   https://www.thingiverse.com/wwrr55
   is licensed under Attribution-ShareAlike 4.0 International. To view a
   copy of this license, visit
   http://creativecommons.org/licenses/by-sa/4.0/
*****************************************************************************/

use <Pulley_Helpers.scad>
use <./libraries/threads.scad> // https://github.com/rcolyer/threads-scad

part=0; // [0:main, 1:support]

teeth = 200;
Azimuth_Bearing_Hub_Diameter_bottom_mm = 25;
Azimuth_Bearing_Clearance_Z_mm = 8;
Azimuth_Bearing_Clearance_Radius_mm = 40;

Hub_lock_screws = false;

Central_Height_z_spacer_mm = 0;
outer_rim_radial_thickness = 5;
number_of_spokes = 8;
pulley_teeth_height_mm = 10.5;
bearing_hole_diameter_mm = 9.9;
hub_extra_height_mm = 4;
hub_lock_screw_hole_diameter_mm = 3.2;
hub_lock_nut_side_mm = 5.9;
hub_lock_nut_thickness_mm = 2.6;
hub_lock_socket_diameter_mm = 6;
module __no_customizer() {}

$fa = $preview ? 20 : 1;
$fs = $preview ? 5 : 0.1;

mm_per_inch = 25.4;

base_height = mm_per_inch / 16;
alt_idler_height = base_height;
alt_base_diameter = 2 + (teeth * 2 / PI);
alt_base_cut_diameter = (teeth * 2 / PI) - 2 * outer_rim_radial_thickness;

Central_Bearing_wall_thickness_mm = 25.4 / 5;
central_height = Central_Height_z_spacer_mm + base_height + alt_idler_height + pulley_teeth_height_mm + hub_extra_height_mm;

echo(str("Full height = ", central_height / mm_per_inch, " in."));

spoke_width_mm = 10;
spoke_rounding_radius_mm = 3;

stlSolidBodymm = 0.01;

if (part == 0)
    main();
else
{
    translate([0, 0, 1])
        cut_space_for_bearing();
}

function rot_angle_from_omit(teeth, omit) = omit * 180 / teeth;

module pulleyBase(teeth, rim_mm, height, omit = 0)
{
    difference()
    {
        // pulley main
        rotate([0, 0, 180 + rot_angle_from_omit(teeth, omit)])
            rotate_extrude(angle = (teeth - omit) * 360 / teeth, $fa = 180 / teeth)
            translate([pully_OD(teeth) / 2 - rim_mm, 0])
                square([rim_mm, height]);
        // cut teeth out of pulley     
        rotate([0, 0, 270 + (omit + 1) * 180 / teeth])
            translate([0, 0, -stlSolidBodymm])
            linear_extrude(height = height + 2 * stlSolidBodymm)
                cut_teeth_from_pulley(teeth, omit = omit);
    }
}

module hub_lock_cuts()
{
    if (Hub_lock_screws)
        rotate([0,90,180 + 180/number_of_spokes])
        {
            cylinder(d=hub_lock_screw_hole_diameter_mm, h=Azimuth_Bearing_Clearance_Radius_mm);
            translate([0,0,bearing_hole_diameter_mm*1.5])
                cylinder(d=hub_lock_socket_diameter_mm, h=Azimuth_Bearing_Clearance_Radius_mm);
            extend_beyond_hub_surface = 10;
            translate([-extend_beyond_hub_surface/2,0,bearing_hole_diameter_mm*.85])
                cube(center=true,[hub_lock_nut_side_mm+extend_beyond_hub_surface, hub_lock_nut_side_mm, hub_lock_nut_thickness_mm]);
        }
}

module cut_space_for_bearing()
{
    translate([0,0,-base_height-.01])
        cylinder(h=Azimuth_Bearing_Clearance_Z_mm, r=Azimuth_Bearing_Clearance_Radius_mm);
}

module main() {
    intersection()
    {
        difference()
        {
            ScrewHole(10, central_height + .02)
            {
                difference()
                {
                    union()
                    {
                        // pulley with teeth
                        pulleyBase(teeth, outer_rim_radial_thickness, pulley_teeth_height_mm);
                        // base
                        translate([0, 0, -base_height])
                            cylinder(h = base_height, d = alt_base_diameter);
                        // idler
                        chamfer = 1.5;
                        rot_profile = [[0, 0], [outer_rim_radial_thickness - chamfer, 0], 
                                [outer_rim_radial_thickness, chamfer], [outer_rim_radial_thickness, alt_idler_height], 
                                [0, alt_idler_height]];
                        translate([0, 0, pulley_teeth_height_mm])
                            rotate_extrude(angle = 360)
                            translate([alt_base_diameter / 2 - outer_rim_radial_thickness, 0])
                            polygon(rot_profile);
                    }
                 }
                translate([0, 0, -base_height])
                {
                    // central bearing
                    difference()
                    {
                        union()
                        {
                            spoke_lift = hub_extra_height_mm + pulley_teeth_height_mm / 2;
                            tilt = atan((2 * spoke_lift)/pully_OD(teeth) );
                            linear_extrude(height = central_height)                              
                                circle(d = Azimuth_Bearing_Hub_Diameter_bottom_mm);
                            translate([0,0, spoke_lift])
                            for (spoke = [0:1 : number_of_spokes - 1])
                            {
                                rotate([0, 0, spoke * 360 / number_of_spokes])
                                {
                                    rotate([0, -90 - tilt, 0])
                                        linear_extrude(height = alt_base_cut_diameter / 2)
                                        translate([0, -spoke_width_mm / 2])
                                        offset(spoke_rounding_radius_mm)
                                        offset(-spoke_rounding_radius_mm)
                                        square([pulley_teeth_height_mm + base_height, spoke_width_mm]);

                                }
                            }
                            spoke_match_radius_mm = Azimuth_Bearing_Clearance_Radius_mm + 6;
                            cylinder(h=3*base_height, r=spoke_match_radius_mm);
                        }
                    }
                }
            } 

            cut_space_for_bearing();
            translate([0,0,-base_height-.01])
            {
                //cylinder(h=central_height + .02, d=bearing_hole_diameter_mm);
                translate([0,0,central_height])
                    cylinder(h=100, r=Azimuth_Bearing_Clearance_Radius_mm);
                translate([0,0,central_height- 1.2 * hub_lock_screw_hole_diameter_mm])
                {
                    hub_lock_cuts();
                    rotate([0,0,90])
                        hub_lock_cuts();
                }
            }
        }
    }
}

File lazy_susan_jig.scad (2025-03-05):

module no_more_customizer() {}
$fa = $preview ? 15 : 1;
$fs = $preview ? 3 : .1;

mmPerInch = 25.4;

mount_hole_diameter_mm = 10 - .1;
mount_brace_diameter_mm = 1 * mmPerInch;
mount_brace_height = mmPerInch * 3/32;
skid_pad_thickness_mm = mmPerInch * .3; 
skid_pad_radial_from_center = 3 * mmPerInch;
spoke_width = 0.5 * mmPerInch;

dolly_ID = 4.74;
dolly_ID_squeeze = dolly_ID - .01;

hole_extrude = max(mount_brace_height, skid_pad_thickness_mm);

difference()
{
    intersection()
    {
    union()
    {
        cylinder(d=mount_brace_diameter_mm, h = mount_brace_height);
        for (r = [0, 120, 240]) rotate([0,0,r])
        difference()
        {
            linear_extrude(height = skid_pad_thickness_mm)
            {
                translate([skid_pad_radial_from_center/2, 0])
                    square([skid_pad_radial_from_center, spoke_width], center = true);
             }
        }
    }
    linear_extrude(height=hole_extrude, scale= dolly_ID_squeeze/dolly_ID)
        circle(d=dolly_ID * mmPerInch);
    }
    translate([0,0,-.1])
        cylinder(d = mount_hole_diameter_mm, h = hole_extrude + .2);
}

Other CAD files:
BatteryPackEnclosure.FCStd
ScopeLevelHolder.FCStd
MicroUSB.FCStd
Azimuth-Bearings-M10-lock.FCStd
OnStepElevationPulley.scad
LV8729.FCStd
M10-nut.FCStd
OnStepGearReducer.scad
OnStepGearboxElevationPulley.scad
OnstepElevationPulley.FCStd
Pulley_Helpers.scad
Pulley_T-MXL-XL-HTD-GT2_N-tooth-thing16627.scad
skid_form.scad

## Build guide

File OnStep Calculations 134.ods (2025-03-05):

 |  |  | OnStep Configuration Calculator |  |  |  |  |  | Version 1.34
 |  |  |  |  |  |  |  |  | Authors:
 | Enter your values in the green areas, results which are outlined have equivalents in OnStep's Config.h file. |  |  |  |  |  |  |  | Howard Dutton
 | Limits are in red, OnStep won't function properly if they aren't adhered too. Other limits are recommendations. Note that “µs” = micro-seconds. |  |  |  |  |  |  |  | Khalid B.
 |  |  |  |  |  |  |  |  | Chris K.
 | Axis1 is for Right Ascension or Azimuth
 | Axis2 is for Declination or Altitude |  |  | AXIS1_DRIVER_ | Gear Reduction
 |  |  | Stepper-Steps | MICROSTEPS | GR1 Ratio | GR2 Ratio
 | AXIS1_STEPS_PER_DEGREE | 9215.0756 | 400 | 32 | 10.0000 | 25.9174 | RA/Azm
 | AXIS2_STEPS_PER_DEGREE | 6911.3067 | 200 | 32 | 15.0000 | 25.9174 | Dec/Alt
 |  | (300 to 122400) |  | AXIS2_DRIVER_ | A timing belt | A worm/wheel
 |  |  |  | MICROSTEPS | reduction for | reduction for
 | PEC_STEPS_PER_WORM_ROTATION | or |  |  | example. | example.
 | AXIS1_STEPS_PER_WORMROT | 96000 |  |  |  |  |  | Slewing motor shaft speeds:
 |  |  |  |  | Tracking resolution (in arc-sec): |  |  | Axis1 | RA/Azm
Micro-step mode switching allows higher slew speeds but larger steps may promote resonance: |  |  |  |  | Calculated | Estimate |  | 86.4 | RPM
 | AXIS1_DRIVER_MICROSTEPS_GOTO | 4 | OFF to disable |  | (servo, etc.) | (stepper typical) |  | 1.4 | RPS
 | AXIS2_DRIVER_MICROSTEPS_GOTO | 2 | OFF to disable | Axis1 | 0.39 | 0.81 | <= 1.25 | 0.6 | kHz (full step)
 | SLEW_RATE_BASE_DESIRED | 2.0 | °/sec | Axis2 | 0.52 | 1.08 | <= 1.25 | Axis2 | Dec/Alt
 |  |  |  |  |  |  |  | 129.6 | RPM
 |  | ↓ |  |  | RA Tracking freq. = 38.396 steps/sec |  |  | 2.2 | RPS
 |  |  |  |  |  |  |  | 0.4 | kHz (full step)
 | Base avg step rate | 631.4 | µs/step → 2°/s slew rate
 | Runtime adjustable, slowest avg step rate | 1262.8 | µs/step → 1°/s slew rate
 | Runtime adjustable, fastest avg step rate | 315.7 | µs/step → 4°/s slew rate |  | * = Approximate rate limit recommendations (in µs/step):
 |  | (see note *) |  |  | Platform |  |  | SQUARE | PULSE
 |  |  |  |  | Mega2560 |  | >= | 48 | 30.0
 | OnStep will limit slew rates automatically if they exceed your platform’s capabilities. |  |  |  | ESP32 |  | >= | 40 | 25.0
 |  |  |  |  | STM32 F103 |  | >= | 34 | 21.3
 |  |  |  |  | STM32 F303, F401, F411 |  | >= | 20 | 12.5
 | Step signaling defaults to STEP_WAVE_FORM SQUARE for best |  |  |  | STM32 F446, Teensy3.2 |  | >= | 14 | 8.8
 | compatibility with step/dir drivers. Using STEP_WAVE_FORM PULSE |  |  |  | Teensy3.5 |  | >= | 12 | 7.5
 | allows 1.6 times faster slew rates. |  |  |  | Teensy3.6 |  | >= | 2.6 | 1.6
 |  |  |  |  | Teensy4.0, T4.1 |  | >= | 1.5 | N/A

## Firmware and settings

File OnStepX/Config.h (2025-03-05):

/* ---------------------------------------------------------------------------------------------------------------------------------
 * Configuration for OnStepX
 *
 *          For more information on setting OnStep up see http://www.stellarjourney.com/index.php?r=site/equipment_onstep 
 *                      and join the OnStep Groups.io at https://groups.io/g/onstep
 * 
 *           *** Read the compiler warnings and errors, they are there to help guard against invalid configurations ***
 *
 * ---------------------------------------------------------------------------------------------------------------------------------
 * ADJUST THE FOLLOWING TO CONFIGURE YOUR CONTROLLER FEATURES ----------------------------------------------------------------------
 * <-Req'd = always must set, <-Often = usually must set, Option = optional, Adjust = adjust as req'd, Infreq = infrequently changed
*/
//      Parameter Name              Value   Default  Notes                                                                      Hint

// =================================================================================================================================
// CONTROLLER ======================================================================================================================

// PINMAP ------------------------------------------------- see https://onstep.groups.io/g/main/wiki/Configuration_Controller#PINMAP
#define PINMAP                        MaxPCB4 //    OFF, Choose from: MiniPCB, MiniPCB2, MaxPCB2, MaxESP3, CNC3, STM32Blue,      <-Req'd
                                          //         MaxSTM3, FYSETC_S6_2, etc.  Other boards and more info. in ~/src/Constants.h

// SERIAL PORT COMMAND CHANNELS --------------------- see https://onstep.groups.io/g/main/wiki/Configuration_Controller#SERIAL_PORTS
#define SERIAL_A_BAUD_DEFAULT        57600 //   9600, n. Where n=9600,19200,57600,115200,230400,460800 (common baud rates.)    Infreq
#define SERIAL_B_BAUD_DEFAULT        57600 //   9600, n. Baud rate as above. See (src/pinmaps/) for Serial port assignments.   Infreq
#define SERIAL_B_ESP_FLASHING         OFF //    OFF, ON Upload ESP8266 WiFi firmware through SERIAL_B with :ESPFLASH# cmd.    Option
#define SERIAL_C_BAUD_DEFAULT         OFF //    OFF, n. Baud rate as above. See (src/pinmaps/) for Serial port assignments.   Infreq
#define SERIAL_D_BAUD_DEFAULT         OFF //    OFF, n. Baud rate as above. See (src/pinmaps/) for Serial port assignments.   Infreq
#define SERIAL_E_BAUD_DEFAULT         OFF //    OFF, n. Baud rate as above. See (src/pinmaps/) for Serial port assignments.   Infreq
#define SERIAL_RADIO                  OFF //    OFF, Use BLUETOOTH or WIFI_ACCESS_POINT or WIFI_STATION (ESP32 only.)         Option

// STATUS --------------------------------------------- see https://onstep.groups.io/g/main/wiki/Configuration_Controller#STATUS_LED
#define STATUS_LED                    OFF //    OFF, Steady illumination if no error, blinks w/error code otherwise.          Option

// RETICLE CONTROL ------------------------------- see https://onstep.groups.io/g/main/wiki/Configuration_Controller#RETICLE_CONTROL
#define RETICLE_LED_DEFAULT           OFF //    OFF, n. Where n=0..255 (0..100%) activates feature sets default brightness.   Option
#define RETICLE_LED_MEMORY            OFF //    OFF, ON Remember reticle brightness across power cycles.                      Option
#define RETICLE_LED_INVERT            OFF //    OFF, ON Inverts control for cases where 0V is max brightness.                 Option

// WEATHER SENSOR --------------------------------- see https://onstep.groups.io/g/main/wiki/Configuration_Controller#WEATHER_SENSOR
#define WEATHER                       OFF //    OFF, BME280 (I2C 0x77,) BME280_0x76, BME280_SPI (see pinmap for CS.)          Option
                                          //         BMP280 (I2C 0x77,) BMP280_0x76, BMP280_SPI (see pinmap for CS.)
                                          //         BME280 or BMP280 for temperature, pressure.  BME280 for humidity also.

// SIGNALING ------------------------------------------- see https://onstep.groups.io/g/main/wiki/Configuration_Controller#SIGNALING
#define STEP_WAVE_FORM             SQUARE // SQUARE, PULSE Step signal wave form faster rates. SQUARE best signal integrity.  Adjust
                                          //         Applies to all axes.

// NON-VOLATILE MEMORY ---------------------------------------- see https://onstep.groups.io/g/main/wiki/Configuration_Controller#NV
#define NV_DRIVER              NV_DEFAULT // NV_DEF, Use platforms default non-volatile device to remember runtime settings.  Option

// =================================================================================================================================
// MOUNT ===========================================================================================================================
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

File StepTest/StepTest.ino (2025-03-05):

static const int Pin_EN_1 = 33;
static const int Pin_EN_2 = 40;
static const int Pin_M0_1 = 37;
static const int Pin_M0_2 = 41;
static const int Pin_M1_1 = 36;
static const int Pin_M1_2 = 13;
static const int Pin_M2_1 = 35;
static const int Pin_M2_2 = 14;
static const int Pin_STP_1 = 38;
static const int Pin_STP_2 = 15;
static const int Pin_DIR1 = 39;
static const int Pin_DIR2 = 16;
static const int Pin_RA_plus = 6;
static const int Pin_RA_minus = 3;
static const int Pin_DE_plus = 5;
static const int Pin_DE_minus = 4;

void setup()
{
    digitalWrite(Pin_M0_1, LOW);
    digitalWrite(Pin_M1_1, LOW);
    digitalWrite(Pin_M2_1, LOW);
    digitalWrite(Pin_STP_1, LOW);
    digitalWrite(Pin_DIR1, LOW);
    pinMode(Pin_EN_1, OUTPUT);
    pinMode(Pin_M0_1, OUTPUT);
    pinMode(Pin_M1_1, OUTPUT);
    pinMode(Pin_M2_1, OUTPUT);
    pinMode(Pin_STP_1, OUTPUT);
    pinMode(Pin_DIR1, OUTPUT);

    digitalWrite(Pin_M0_2, LOW);
    digitalWrite(Pin_M1_2, LOW);
    digitalWrite(Pin_M2_2, LOW);
    digitalWrite(Pin_STP_2, LOW);
    digitalWrite(Pin_DIR2, LOW);
    pinMode(Pin_EN_2, OUTPUT);
    pinMode(Pin_M0_2, OUTPUT);
    pinMode(Pin_M1_2, OUTPUT);
    pinMode(Pin_M2_2, OUTPUT);
    pinMode(Pin_STP_2, OUTPUT);
    pinMode(Pin_DIR2, OUTPUT);

    digitalWrite(Pin_EN_1, HIGH);
    digitalWrite(Pin_EN_2, HIGH);

    pinMode(Pin_RA_plus, INPUT);
    pinMode(Pin_RA_minus, INPUT);
    pinMode(Pin_DE_plus, INPUT);
    pinMode(Pin_DE_minus, INPUT);

   pinMode(LED_BUILTIN, OUTPUT);
   digitalWrite(LED_BUILTIN, LOW);
   Serial.begin(9600);
   Serial.write("Testing LV8729 and ST4\r\n");
}

uint8_t st4Read(uint8_t v, int pin)
{
    v <<= 1;
    if (digitalRead(pin) == HIGH)
        v |= 1;
    return v;
}

void loop()
{
    auto now = millis();
    static auto lasttime = now;
    static bool flash = true;
    static uint8_t prev_ST4_Pins = 0xFF;
    static bool Use_ST4 = false;

    if (flash && (now - lasttime > 1000))
    {
        lasttime = now;
        digitalWrite(LED_BUILTIN, digitalRead(LED_BUILTIN) == LOW ? HIGH : LOW);
    }

    uint8_t ST4_pins = 0;
    enum class ST4 {NONE, DE_minus = 1, DE_plus = 2, RA_minus = 4, RA_plus = 8};
    ST4_pins = st4Read(ST4_pins, Pin_RA_plus);
    ST4_pins = st4Read(ST4_pins, Pin_RA_minus);
    ST4_pins = st4Read(ST4_pins, Pin_DE_plus);
    ST4_pins = st4Read(ST4_pins, Pin_DE_minus);

    auto stat = (uint8_t)(0xfu & ~ST4_pins);

    if (ST4_pins != prev_ST4_Pins)
    {
        Serial.write("ST4 change 0x");
        Serial.println(stat, HEX);
        prev_ST4_Pins = ST4_pins;
    }

    if (stat & static_cast<unsigned>(ST4::DE_plus))
        digitalWrite(Pin_DIR1, HIGH);
    else if (stat & static_cast<unsigned>(ST4::DE_minus))
        digitalWrite(Pin_DIR1, LOW);

    if (stat & (static_cast<unsigned>(ST4::DE_plus) | static_cast<unsigned>(ST4::DE_minus)))
    {
        auto prev = digitalRead(Pin_STP_1) == HIGH;
        digitalWrite(Pin_STP_1, prev ? LOW : HIGH);
        delayMicroseconds(700);
    }

    if (stat & static_cast<unsigned>(ST4::RA_plus))
        digitalWrite(Pin_DIR2, HIGH);
    else if (stat & static_cast<unsigned>(ST4::RA_minus))
        digitalWrite(Pin_DIR2, LOW);

    if (stat & (static_cast<unsigned>(ST4::RA_plus) | static_cast<unsigned>(ST4::RA_minus)))
    {
        auto prev = digitalRead(Pin_STP_2) == HIGH;
        digitalWrite(Pin_STP_2, prev ? LOW : HIGH);
        delayMicroseconds(700);
    }


    while (Serial.available() > 0)
    {
        auto c = Serial.read();
        if (c == 'S')
        {
             bool prev = false;
             Serial.write("start\r\n");
             int turns = 400;
             for (int i = 0; i < turns *5; i++)
             {
                digitalWrite(Pin_STP_1, prev ? HIGH : LOW);   
                delayMicroseconds(700);
                prev = !prev;  
             }        
             Serial.write("done\r\n");
 
        } 
        else if (c == 'U')
        {
            bool prev = digitalRead(Pin_EN_1) == LOW;
            digitalWrite(Pin_EN_1, prev ? HIGH : LOW);
            digitalWrite(Pin_EN_2, prev ? HIGH : LOW);
            Serial.write("Enable is now ");
            Serial.write(prev ? "off\r\n" : "on\r\n" );
        }
        else if (c == 'F')
        {
            flash = !flash;
            digitalWrite(LED_BUILTIN, flash ? HIGH : LOW);
        }
        else if (c == 'D')
        {
            bool prev = digitalRead(Pin_DIR1) == LOW;
            digitalWrite(Pin_DIR1, prev ? HIGH : LOW);
            Serial.write("Dir is ");
            Serial.write(prev ? "high\r\n" : "low\r\n");
        }
        else if (c == '4')
            Use_ST4 = !Use_ST4;
    }

}

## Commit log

2025-03-05 model sources
    [Azimuth-Bearing-Holder.FCStd, Azimuth-Bearings-M10-lock.FCStd, Azimuth-Bearings.scad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]
2025-03-06 correct bearing part number
    [OnStepGearReducer.scad]
